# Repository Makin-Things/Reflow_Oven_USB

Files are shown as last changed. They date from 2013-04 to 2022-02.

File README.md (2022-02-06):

# Reflow Oven USB
This project converts a Mini Bake & Grill to be used as a reflow oven for soldering surfae mount pcb's. The oven was chosen for it's compact size but high power elements for its size. the even has been rewired to run both the top and bottom elements at the same time.

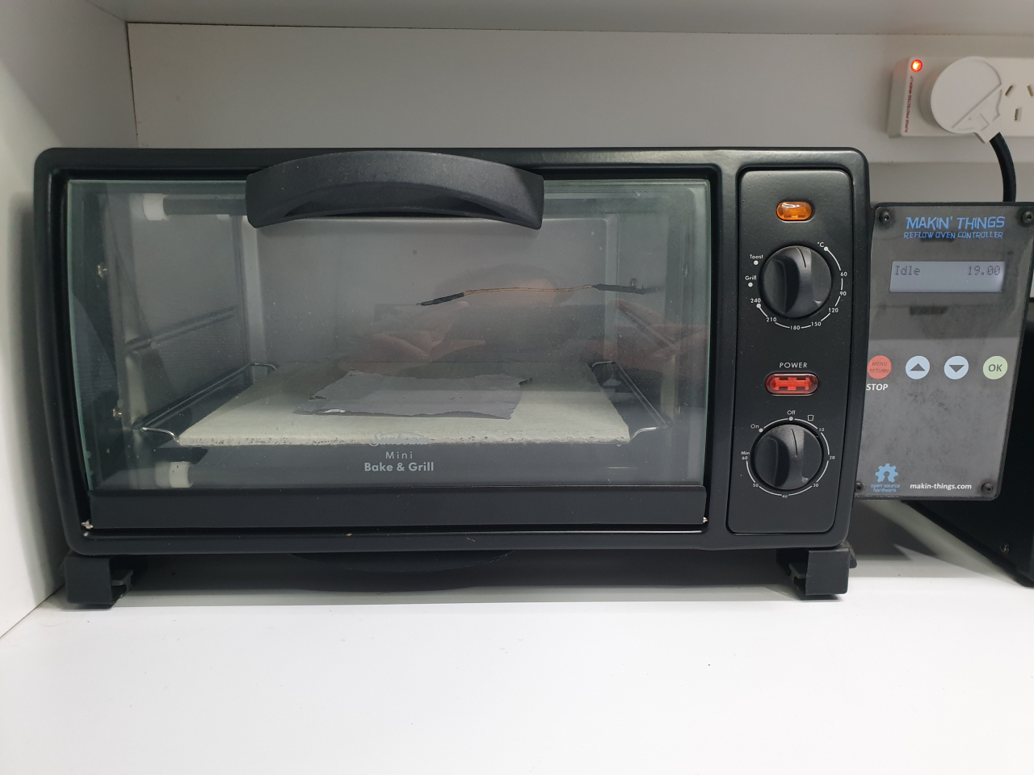
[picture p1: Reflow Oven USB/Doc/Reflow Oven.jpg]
Reflow Oven


The controller has a USB port to allow for firmware updates and monitoring/graphing of the oven while it is running profiles. See seperate repository SMD_Profiler for more information.

## Schematics

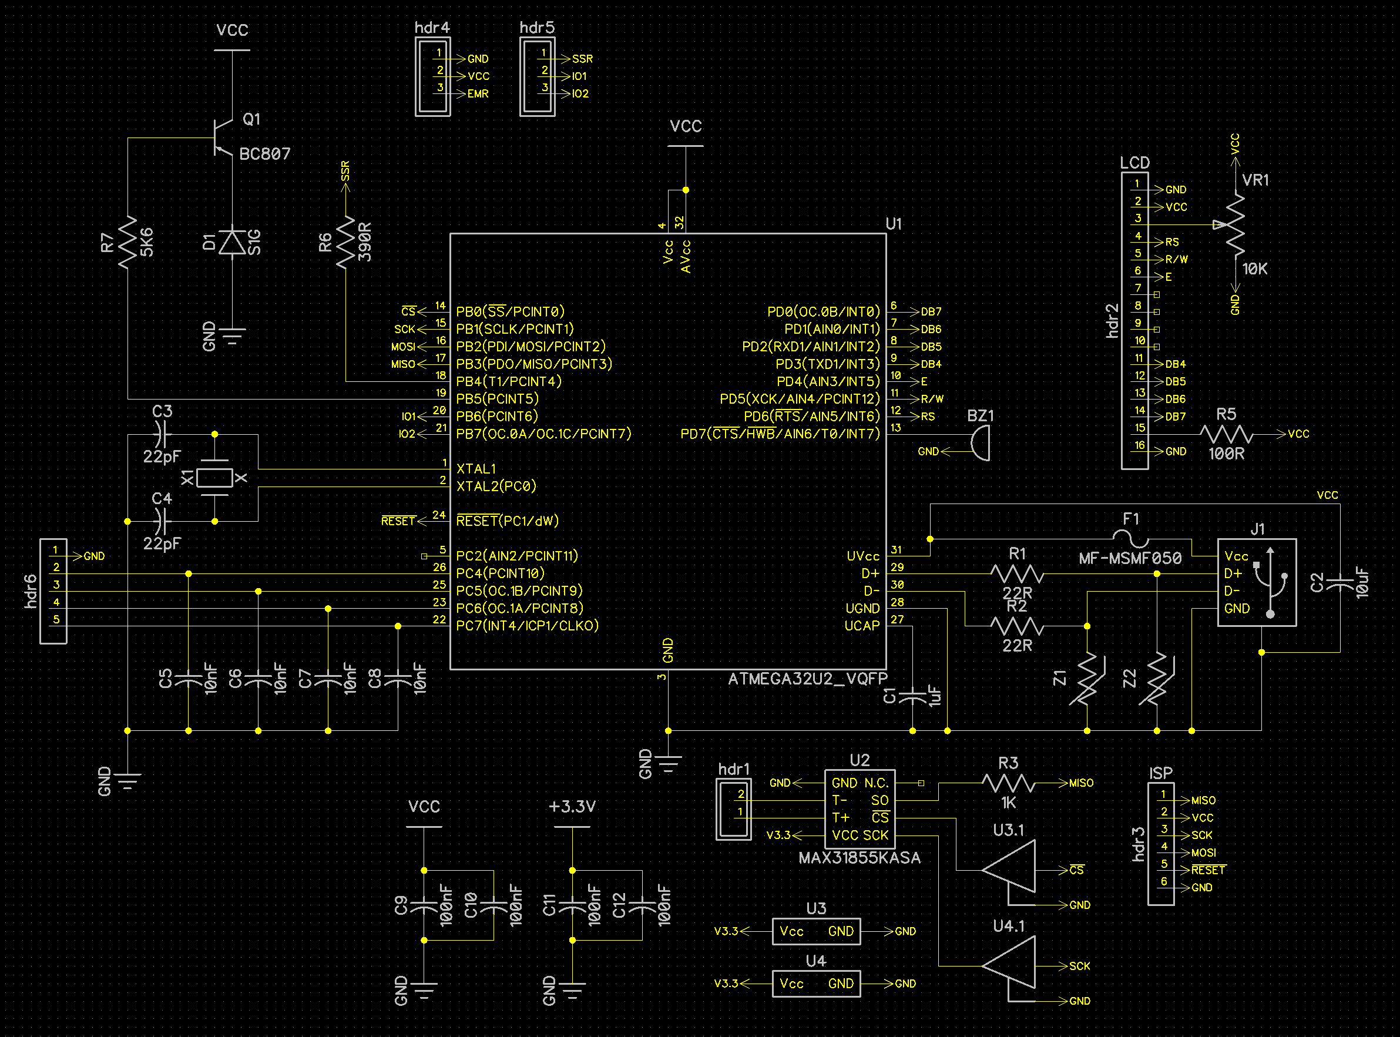
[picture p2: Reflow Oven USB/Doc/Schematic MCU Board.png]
MCU Board


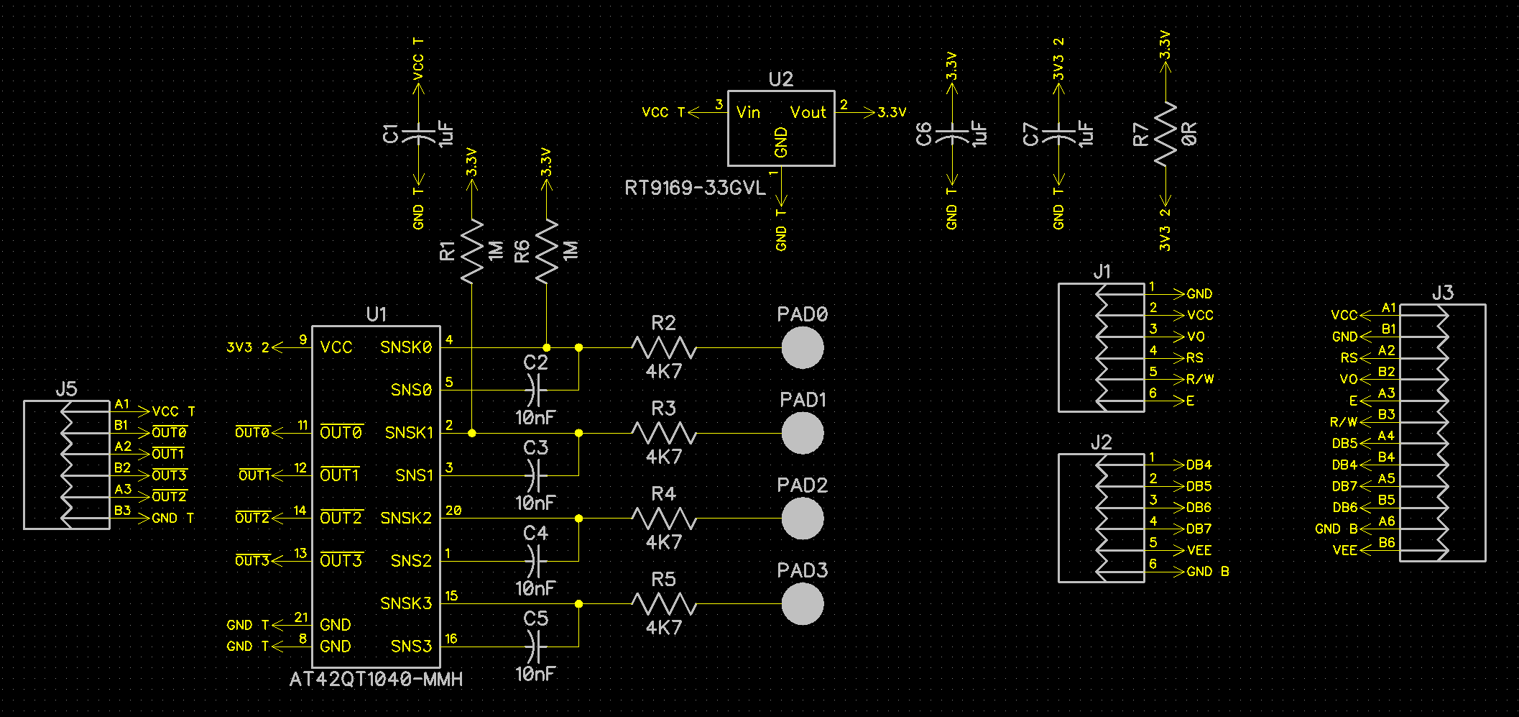
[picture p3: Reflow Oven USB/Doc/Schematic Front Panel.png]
Front Panel


## PCB Layouts

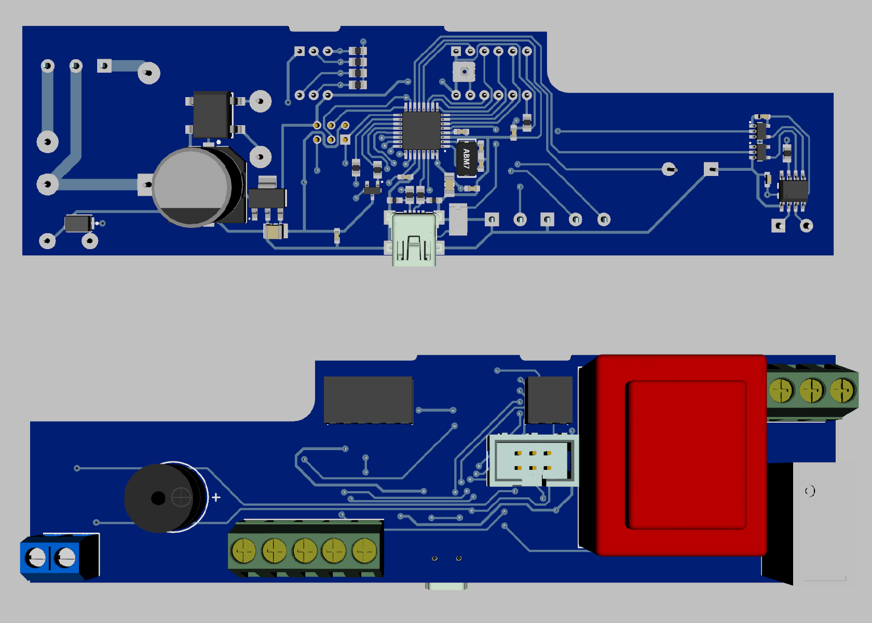
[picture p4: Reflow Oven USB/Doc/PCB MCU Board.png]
MCU Board


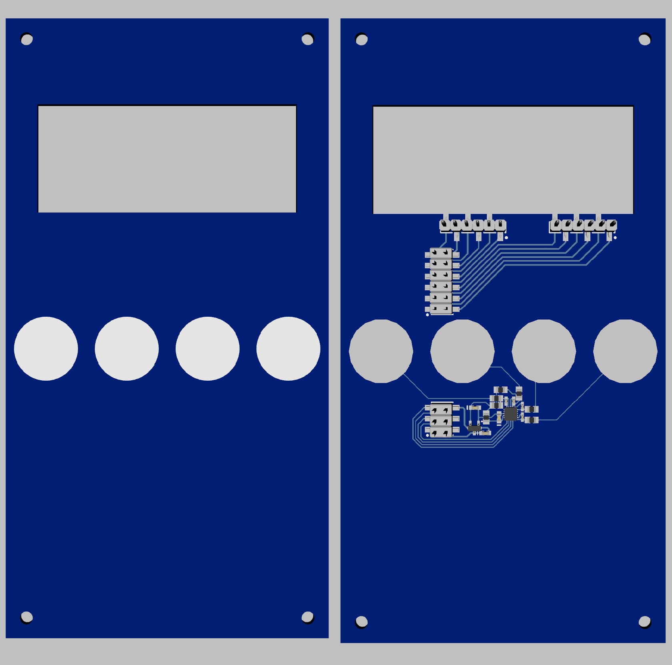
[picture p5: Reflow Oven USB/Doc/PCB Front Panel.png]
Front Panel


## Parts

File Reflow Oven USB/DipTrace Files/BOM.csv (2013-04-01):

RefDes | Type | Value | Part No
BZ1 | Buzzer |  | China
C1 | CAP_0603 | 1uF | E-9527699
C2 | CAP | 10uF | E-1639946
C3 | CAP_0603 | 22pF | E-1414622
C4 | CAP_0603 | 22pF | E-1414622
C5 | CAP_0603 | 10nF | E-1414609
C6 | CAP_0603 | 10nF | E-1414609
C7 | CAP_0603 | 10nF | E-1414609
C8 | CAP_0603 | 10nF | E-1414609
C9 | CAP_0603 | 100nF | E-1288255
C10 | CAP_0603 | 100nF | E-1288255
D1 | S1G |  | E-9843850
hdr1 | Screw Terminal2 |  | China
hdr2 | Hdr16 | LCD | E-3418479
hdr3 | Hdr2x3 | ISP | E-1348883
hdr4 | Screw Terminal3 |  | China
hdr5 | Screw Terminal3 |  | China
hdr6 | Hdr5 |  | Jaycar
J1 | USB Socket |  | E-1696539
J2 | JUMPER
Q1 | BC807 |  | E-1081219
R1 | RES_0805 | 22R | E-1738936
R2 | RES_0805 | 22R | E-1738936
R3 | RES_0805 | 1K | Jaycar
R4 | RES_0805 | 1K | Jaycar
R5 | RES_0805 | 8R2 | Jaycar
R6 | RES_0805 | 390R | Jaycar
R7 | RES_0805 | 5K6 | Jaycar
U1 | ATMEGA32U2_VQFP |  | E-1748524
U2 | MAX6675 |  | China
VR1 | POT | 10K | E-1689863
X1 | CRYSTAL | 8MHz | E-1812391

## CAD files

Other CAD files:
Inventor/Reflow Oven USB Hole.dwg
Inventor/Front Panels Polycarbonate.dwg
Inventor/Reflow Oven Mounting Holes.dwg
Inventor/Front Panels PCB.dwg
Inventor/Board.ipt
Inventor/Complete Reflow Oven.iam
Inventor/Imported Components/NHD-0216HZ/NHD-0216HZ.ipt
Inventor/Imported Components/Reflow Front/Board.ipt
Inventor/Imported Components/Reflow Front/Model_2.ipt
Inventor/Imported Components/Reflow Front/Model_5.ipt
Inventor/Imported Components/Reflow Front/Model_7.ipt
Inventor/Imported Components/Reflow Front/Reflow Front.iam
Inventor/Imported Components/Reflow Front/cap_0402.ipt
Inventor/Imported Components/Reflow Front/cap_0603.ipt
Inventor/Imported Components/Reflow Front/qfn-20_3x3x0.4.ipt
Inventor/Imported Components/Reflow Front/res_0805.ipt
Inventor/Imported Components/Reflow Front/sot23.ipt
Inventor/Imported Components/Reflow MCU/395443002.ipt
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

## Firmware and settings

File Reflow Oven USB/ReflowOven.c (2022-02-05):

//==============================================================================================================================
// U S B   R E F L O W   O V E N   C O N T R O L L E R
//
// Copyright	: 2011 ProAtomic Software Development Pty Ltd
// File Name	: "Reflow.c"
// Title 			: USB Reflow Oven Controller
// Date 			: 18 Jul 2011
// Version 		: 1.00
// Target MCU : ATMEGA32U2
// Author			: Simon Ratcliffe


//==============================================================================================================================
// Description of port usage
//
// Port/Bit	Direction	Usage
// --------	---------	----------------------------------------------------------------------------------------------------------
// B.0			Output		SPI SS for MAX6675
// B.1			Output		SPI Clock to MAX6675				(SCK)
// B.2			Output																(MOSI)
// B.3			Input			SPI Input from MAX6675			(MISO)
// B.4			Output		Dynamic Element Control (SSR)
// B.5			Output		Oven Power Cuttoff (EMR)
// B.6			Output		Spare output
// B.7			Output		Spare output
//
// C.4			Input			Switch 1
// C.5			Input			Switch 2
// C.6			Input			Switch 3
// C.7			Input			Switch 0
//
// D.0			Output		LCD DB4
// D.1			Output		LCD DB5
// D.2			Output		LCD DB6
// D.3			Output		LCD DB7
// D.4			Output		LCD RS
// D.5			Output		LCD R/W
// D.6			Output		LCD E
// D.7			Output		Buzzer

//==============================================================================================================================
// Includes

#include <avr/io.h>
#include <avr/wdt.h>
#include <avr/power.h>
#include <avr/interrupt.h>
#include <avr/pgmspace.h>
#include <string.h>
#include <stdio.h>
#include <stdlib.h>

#include "Descriptors.h"
#include "../LUFA/LUFA/Version.h"
#include "../LUFA/LUFA/Drivers/USB/USB.h"

#include "ReflowOven.h"
#include "lcd.h"
#include "spi.h"
#include "menu.h"
#include "pid.h"
//#include "version.h"

//==============================================================================================================================
// Protect against initial watchdog timeouts

void get_mcusr(void) __attribute__((naked)) __attribute__((section(".init3")));

void get_mcusr(void)
{
	MCUSR = 0;
	wdt_disable();
}

//==============================================================================================================================
// External variables

extern uint8_t CurrentMenuItemIdx;

//==============================================================================================================================
// Defines

#define buildstr "34"

#define OVEN_RELAY_SSR		PB4
#define OVEN_RELAY_EMR		PB5

#define EMR_ON						PORTB &= ~_BV(OVEN_RELAY_EMR)
#define EMR_OFF						PORTB |= _BV(OVEN_RELAY_EMR)

#define SSR_ON						PORTB |= _BV(OVEN_RELAY_SSR)
#define SSR_OFF						PORTB &= ~_BV(OVEN_RELAY_SSR)

//==============================================================================================================================
// Typedefs

typedef struct
{
	char name[PROFILE_NAME_LEN];
	unsigned char calibrated;
	unsigned char preheat_temp;
	unsigned char soak_dutycycle;
	unsigned char soak_rate;
	unsigned char soak_time;
	unsigned char soak_temp;
	unsigned char reflow_time;
	unsigned char reflow_temp;
	unsigned char preheat_cutoff;
	unsigned char reflow_cutoff;
} __profile;

//==============================================================================================================================
// EEPROM Variables and Data

uint8_t __attribute__((section(".validapp"))) ValidApp = 0xBB;

uint8_t EEMEM OvenCalibrated = 1;
uint8_t EEMEM ProfileCount = 3;

__profile EEMEM Profiles[MAX_PROFILES] = 
{
	{"Default         ",1,150,8,8,60,180,60,215,131,206},			  // for small low density boards
	{"Bigger Board    ",1,150,6,8,120,180,90,215,138,206},			// for larger high density boards
	{"Leadfree        ",1,150,12,8,120,200,120,255,138,248} 
};

//__profile EEMEM Profiles[MAX_PROFILES] = {{"Leadfree",1,150,3,2,200,120,255,138,248}}; //perfect for leaded solder
// original production profile that was used in the first 2 years __profile EEMEM Profiles[MAX_PROFILES] = {{"Default",1,150,2,4,180,90,215,124,204}};
// setup __profile EEMEM Profiles[MAX_PROFILES] = {{"Default",0,150,2,4,180,90,220,0,0}};
// 210 reflow __profile EEMEM Profiles[MAX_PROFILES] = {{"Default",1,150,2,4,180,90,210,123,199}};

uint8_t EEMEM TempCounts[20] = {18,14,14,15,11,10,11,11,10,12,11,12,12,11,12,13,18,15,16,16};
uint16_t EEMEM FinalTemps[20] = {77,117,153,185,213,237,257,0,0,0,0,0,0,0,0,0,0,0,0,0};

//==============================================================================================================================
// PROGMEM Menu definition

const MENU_ITEM ShowReflowMenu[];
const MENU_ITEM SettingsMenu[];
const MENU_ITEM SelectProfileMenu[];

const char Str00[] PROGMEM = "Main menu       ";
const char Str01[] PROGMEM = "Reflow          ";
const char Str02[] PROGMEM = "Settings        ";

const MENU_ITEM MainMenu[] PROGMEM = 
{
	{MENU_ITEM_TYPE_MAIN_MENU_HEADER, Str00, (PGM_P)SetIdleMode},
	{MENU_ITEM_TYPE_SUB_MENU, Str01, (PGM_P)ShowReflowMenu},
	{MENU_ITEM_TYPE_SUB_MENU, Str02, (PGM_P)SettingsMenu},
	{MENU_ITEM_TYPE_END_OF_MENU, NULL, 0}
};

const char Str10[] PROGMEM = "Reflow          ";
const char Str11[] PROGMEM = "Run             ";
const char Str12[] PROGMEM = "Select Profile  ";
const char Str13[] PROGMEM = "Edit Profile    ";

const MENU_ITEM ShowReflowMenu[] PROGMEM =
{	
	{MENU_ITEM_TYPE_SUB_MENU_HEADER, Str10, (PGM_P)MainMenu},
	{MENU_ITEM_TYPE_COMMAND, Str11, (PGM_P)RunProfileCommand},
	{MENU_ITEM_TYPE_SUB_MENU, Str12, (PGM_P)SelectProfileMenu},
	{MENU_ITEM_TYPE_COMMAND, Str13, (PGM_P)EditProfileCommand},
	{MENU_ITEM_TYPE_END_OF_MENU, NULL, 0}
};

const char Str200[] PROGMEM = "Select Profile  ";

const MENU_ITEM SelectProfileMenu[] PROGMEM =
{
	{MENU_ITEM_TYPE_SUB_MENU_HEADER, Str200, (PGM_P)ShowReflowMenu},
	{MENU_ITEM_TYPE_EEMEM_COMMAND, (PGM_P)MenuGetEEMEMItem, (PGM_P)SelectProfileCommand}
};	

const char Str20[] PROGMEM = "Settings        ";
const char Str21[] PROGMEM = "Calib. Oven     ";
const char Str22[] PROGMEM = "PID Test        ";
const char Str23[] PROGMEM = "Calib. Profile  ";
const char Str24[] PROGMEM = "Calib. 60c      ";
const char Str25[] PROGMEM = "Calib. 120c     ";

const MENU_ITEM SettingsMenu[] PROGMEM =
{
	{MENU_ITEM_TYPE_SUB_MENU_HEADER, Str20, (PGM_P)MainMenu},
	{MENU_ITEM_TYPE_COMMAND, Str21, (PGM_P)CalibrateOvenCommand},
	{MENU_ITEM_TYPE_COMMAND, Str22, (PGM_P)PIDTestCommand},
	{MENU_ITEM_TYPE_COMMAND, Str23, (PGM_P)CalibrateProfileCommand},
	{MENU_ITEM_TYPE_COMMAND, Str24, (PGM_P)Calibrate60cCommand},
	{MENU_ITEM_TYPE_COMMAND, Str25, (PGM_P)Calibrate120cCommand},
	{MENU_ITEM_TYPE_END_OF_MENU, NULL, 0}
};

// Oven calibration stages

// Profile calibration stages

// Reflow stages

//==============================================================================================================================
// Global Variables

USB_ClassInfo_CDC_Device_t VirtualSerial_CDC_Interface =
{
	.Config =
	{
		.ControlInterfaceNumber   = 0,
		.DataINEndpoint           =
		{
			.Address          = CDC_TX_EPADDR,
			.Size             = CDC_TXRX_EPSIZE,
			.Banks            = 1,
		},
		.DataOUTEndpoint =
		{
			.Address          = CDC_RX_EPADDR,
			.Size             = CDC_TXRX_EPSIZE,
			.Banks            = 1,
		},
		.NotificationEndpoint =
		{
			.Address          = CDC_NOTIFICATION_EPADDR,
			.Size             = CDC_NOTIFICATION_EPSIZE,
			.Banks            = 1,
		},
	},
};

static FILE USBSerialStream;
char inBuf[80];
char tmpStr[17];
char profileName[PROFILE_NAME_LEN];
uint8_t currentProfile = 1;
bool usbConnected = false;
bool isRunning = false;
bool showTemp = true;
uint32_t ovenTempAccum = 0;
uint16_t ovenTemp;
uint16_t ovenEndTemp;
uint16_t ovenTempArray[68];
uint16_t ovenDelta4Array[12] = {0xFFFF};
int16_t ovenDelta4;
int16_t ovenDelta16;
int16_t ovenDelta32;
int16_t ovenRateOfChange;
uint8_t deltaCount = 0;
uint8_t ovenStage; // Used to store where a task is up to
uint16_t ovenCounter;
int16_t ovenError = 0;
void(*ProcessHandler)();
uint16_t count = 0;
uint16_t endCount = 3600;
uint8_t endSet = 0;
__profile profile;
volatile uint8_t tick = 0;
volatile bool readtick = 0;
volatile uint8_t subtickCounter = 0;
volatile uint8_t duty_cycle = 0;
uint8_t readings = 0;
bool lcdPresent = true;
uint8_t buttons = 0;
uint8_t newButton;
PIDController pid;

//==============================================================================================================================
// Interrupt routines

ISR (TIMER1_COMPA_vect)
{
	subtickCounter++;
	if (subtickCounter == 100)
	{
		subtickCounter = 0;
	}

	if ((subtickCounter % 10) == 0)
	{
		readtick = ((subtickCounter % 10) == 0);
	}

  if ((subtickCounter == 0) || (subtickCounter == 50))
	{
		tick++;
	}
	
	if ((duty_cycle > 0) && (duty_cycle < 100))
	{
		if (subtickCounter == duty_cycle)
		{
			SSR_OFF;
		}
		else if (subtickCounter == 0)
		{
			SSR_ON;
		}
	}
}

//==============================================================================================================================
// Get the menu item at a given index from EEMEM

void MenuGetEEMEMItem(uint8_t idx)
{
	eeprom_read_block ((void*)&profileName, (const void*)&Profiles[idx-1], PROFILE_NAME_LEN);
}

//==============================================================================================================================
// Event handler for the library USB Connection event

void EVENT_USB_Device_Connect(void)
{
	usbConnected = true;
}

//==============================================================================================================================
// Event handler for the library USB Disconnection event

void EVENT_USB_Device_Disconnect(void)
{
	usbConnected = false;
}

//==============================================================================================================================
// Event handler for the library USB Configuration Changed event

void EVENT_USB_Device_ConfigurationChanged(void)
{
	bool ConfigSuccess = true;

	ConfigSuccess &= CDC_Device_ConfigureEndpoints(&VirtualSerial_CDC_Interface);
}

//==============================================================================================================================
// Event handler for the library USB Control Request reception event

void EVENT_USB_Device_ControlRequest(void)
{
	CDC_Device_ProcessControlRequest(&VirtualSerial_CDC_Interface);
}

//==============================================================================================================================
// Functions

uint8_t GetPacket(char* buf, uint8_t size)
{
	if (CDC_Device_BytesReceived(&VirtualSerial_CDC_Interface))
	{
		fgets(buf, size, &USBSerialStream);
//		printf("$$%s$$\n", buf);
		while ((strlen(buf) > 0) && ((buf[strlen(buf)-1] == '\r') || (buf[strlen(buf)-1] == '\n')))
		{
			buf[strlen(buf)-1] = 0;
		}
//		printf("##%s##\n", inBuf);
		return true;
	}
	
	return false;
}

//==============================================================================================================================
// Configure the various bits of hardware

void SetupHardware(void)
{
	// Configure IO Ports
	PORTB = _BV(OVEN_RELAY_EMR); // Turn off the EMR relay
	DDRB |= _BV(OVEN_RELAY_SSR) | _BV(OVEN_RELAY_EMR); // Relay outputs
	DDRD |= _BV(PD7); // Buzzer as output
	PORTC = 0xF0; // Enable pullups on for switches

	// Initialise SPI
  spi_init ();

	//Initialise LCD
  if (!lcd_init (LCD_DISP_ON)) // Initialise the LCD
  {
	  lcdPresent = false;
  }

	// USB Hardware Initialization
	USB_Init();
	
	// Setup Timer/Counter1
	TCCR1A = 0;
	TCCR1B = (1 << WGM12) | (1 << CS11) | (1 << CS10);
	OCR1A = 1250; // = 0.01 seconds
//	OCR1A = 6250; // = 0.05 seconds
//	OCR1A = 12500; // = 0.1 seconds
//	OCR1A = 62500; // = 0.5 seconds
	TIMSK1 = (1 << OCIE1A);
}

//==============================================================================================================================
// Read temperature
uint16_t ReadTemp ()
{
  return spi_read();	
}


//==============================================================================================================================
// Send a temperature packet

void UpdateTemp (void)
{
	char str[20];

	ovenTemp = ovenTempAccum>>2;
	ovenTempAccum = 0;
	
	if (ovenTempArray[0] == 0)
	{
		for (uint8_t i = 0; i < 68; i++)
		{
			ovenTempArray[i] = ovenTemp;
		}
	}
	else
	{
		memmove(&ovenTempArray[1], &ovenTempArray[0], sizeof(uint16_t)*67);
		ovenTempArray[0] = ovenTemp;
	}
	
	ovenDelta4 = (int16_t)(ovenTempArray[0]+ovenTempArray[1]+ovenTempArray[2]+ovenTempArray[3]-ovenTempArray[8]-ovenTempArray[9]-ovenTempArray[10]-ovenTempArray[11]);
	ovenDelta16 = (int16_t)(ovenTempArray[0]+ovenTempArray[1]+ovenTempArray[2]+ovenTempArray[3]-ovenTempArray[32]-ovenTempArray[33]-ovenTempArray[34]-ovenTempArray[35]);
	ovenDelta32 = (int16_t)(ovenTempArray[0]+ovenTempArray[1]+ovenTempArray[2]+ovenTempArray[3]-ovenTempArray[64]-ovenTempArray[65]-ovenTempArray[66]-ovenTempArray[67]);

	if (ovenDelta4Array[0] == 0xFFFF)
	{
		for (uint8_t i = 0; i < 12; i++)
		{
			ovenDelta4Array[i] = ovenDelta4;
		}
	}
	else
	{
		memmove(&ovenDelta4Array[1], &ovenDelta4Array[0], sizeof(uint16_t)*11);
		ovenDelta4Array[0] = ovenDelta4;
	}
	
	ovenRateOfChange = (int16_t)(ovenDelta4Array[0]+ovenDelta4Array[1]+ovenDelta4Array[2]+ovenDelta4Array[3]-ovenDelta4Array[8]-ovenDelta4Array[9]-ovenDelta4Array[10]-ovenDelta4Array[11]);

	if (lcdPresent)
	{
		lcd_gotoxy(10, 0);
	}

	if (ovenTemp >= 65533)
	{
	  setDutyCycle(0); //Turn off SSR
	  _delay_ms(25); //Wait for SSR to power down
	  EMR_OFF; // Turn off EMR
		if (ovenTemp == 65535)
		{
			sprintf_P (str, PSTR("No TC "));
		}
		else if (ovenTemp == 65534)			
		{
			sprintf_P (str, PSTR("SG Err"));
		}
		else
		{
			sprintf_P (str, PSTR("SV Err"));
		}
		if ((lcdPresent) && (showTemp))
		{
			lcd_puts (str);
		}		
		fprintf (&USBSerialStream, "%u,%u,%s\n", ovenStage, count, str);
	}
	else
	{
		sprintf_P (str, PSTR("%3u.%02u"), ovenTemp>>2, (ovenTemp & 0x03)*25);
		if ((lcdPresent) && (showTemp))
		{
			lcd_puts (str);
		}
		fprintf_P (&USBSerialStream, PSTR("%u,%u,%s,%u, %d,%d,%d, %d,%d\n"), ovenStage, count, str, duty_cycle, ovenDelta4, ovenDelta16, ovenDelta32, ovenRateOfChange, ovenError);
	}

	count++;
}

//==============================================================================================================================
// Send the oven settings

void SendOvenSettings(void)
{
	char ReportString[80];
	
	sprintf_P(ReportString, PSTR("=OGET,%u,%u,%u"), eeprom_read_byte(&OvenCalibrated), MAX_PROFILES, eeprom_read_byte(&ProfileCount));
	for (uint8_t i = 0; i < 20; i++)
	{
		sprintf_P(tmpStr, PSTR(",%u"), eeprom_read_byte(&TempCounts[i]));
		strcat(ReportString, tmpStr);
	}
	
	strcat(ReportString,"\n");
	
	// Write the string to the virtual COM port via the created character stream
	fputs(ReportString, &USBSerialStream);
}

//==============================================================================================================================
// Cleanup and jump into the bootloader

void Bootloader(void)
{
	lcd_clrscr();
	lcd_puts_P("Bootloader");
//	wdt_disable();
	TIMSK1 = 0; // Disable TIMER1
	USB_Detach();
	_delay_ms(1000);
	eeprom_write_byte(&ValidApp, 0xFF);
	while (!eeprom_is_ready());
	wdt_enable(WDTO_30MS);
	for (;;);
}

//==============================================================================================================================
//

void setDutyCycle (uint8_t ratio)
{
	duty_cycle = ratio;
	if (duty_cycle == 0)
	{
		SSR_OFF;
	}
	if (duty_cycle == 100)
	{
		SSR_ON;
	}
}

//==============================================================================================================================
//

uint8_t getDutyCycle(uint16_t temp)
{
	uint8_t i;
	
	for (i = 0; i < 20; i++)
	{
		if (temp <= eeprom_read_word(&FinalTemps[i]))
		{
			return (i+1)*5;
		}
	}
	return 0;
}

//==============================================================================================================================
//

void printProfile (void)
{
	fprintf (&USBSerialStream, "=RUN,%s,%u,%u,%u,%u,%u,%u,%u,%u\n",
		profile.name, profile.preheat_temp, profile.soak_dutycycle*5, profile.soak_temp, profile.reflow_time, profile.reflow_temp, profile.calibrated,
		profile.preheat_cutoff, profile.reflow_cutoff);
}

//==============================================================================================================================
//

void RunProfileCommand()
{
	lcd_gotoxy(0, 1);
	lcd_puts_P("                ");
	showTemp = true;
	ovenStage = 0;
	count = 0;
	ProcessHandler = RunProfileHandler;
	isRunning = true;
};

//==============================================================================================================================
//

void RunProfileHandler()
{
	switch (ovenStage)
	{
		case 0: // close door & start message
			lcd_gotoxy(0, 1);
			lcd_puts_P("Close door      ");
			ovenStage++;
			break;

		case 1: // wait for button press
			if ((newButton) && (buttons == EVENT_ENTER_BUTTON_PUSHED))
			{
				ovenStage++;
			}
			break;

		case 2: // Preheat
			printProfile(); // Send the profile we are about to run to the serial port
			lcd_gotoxy(0, 1);
			lcd_puts_P("Preheat         ");
			count = 0;
			EMR_ON; //Turn on the EMR
			_delay_ms(25);
			setDutyCycle(100); //Turn on the SSR
			ovenStage++;
			break;

		case 3: // Reached preheat cutoff
//			if ((ovenTemp >> 2) >= profile.preheat_cutoff)
			if ((ovenTemp) >= ((profile.preheat_temp << 2) - ovenDelta4))
			{
				lcd_gotoxy(0, 1);
				lcd_puts_P("Preheat cutoff  ");
				setDutyCycle(getDutyCycle(profile.preheat_temp)-5); //Reduce the output power
				ovenStage++;
			}
			break;

		case 4: // Wait for the oven to reach the preheat temp
			if ((ovenTemp >> 2) >= profile.preheat_temp)
			{
				lcd_gotoxy(0, 1);
				lcd_puts("Soak            ");
				ovenCounter = 0;
				ovenStage++;
			}
			break;

		case 5:
			if (tick)
			{
				ovenCounter++;
				ovenError = (int16_t)(ovenTemp-(((uint16_t)(profile.preheat_temp) << 2)+(((uint16_t)profile.soak_temp-(uint16_t)profile.preheat_temp) << 2)*((float)(ovenCounter)/((uint16_t)profile.soak_time << 1))));
				
				if (ovenError > 8) // rate to high, reduce duty cycle
				{
					setDutyCycle(getDutyCycle(profile.soak_temp));
				}
				else
				{
					setDutyCycle(getDutyCycle(profile.soak_temp)+abs(ovenError-12)*5/4);
				}

				if ((ovenTemp >> 2) >= profile.soak_temp)
				{
					setDutyCycle(100);
					lcd_gotoxy(0, 1);
					lcd_puts_P("Reflow          ");
					ovenCounter = count;
					ovenError = 0;
					ovenStage++;
				}
			}
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
int main(void)
{
	SetupHardware();
	
	// Create a regular character stream for the interface so that it can be used with the stdio.h functions
	CDC_Device_CreateStream(&VirtualSerial_CDC_Interface, &USBSerialStream);

	sei();

	if (lcdPresent)
	{
	  lcd_clrscr(); // clear display and home cursor
		lcd_puts_P("Reflow Oven USB\nv2."buildstr);
	}

	for (;;)
	{
		if (tick == 6)
		{
			if (lcdPresent)
			{
				lcd_clrscr(); // clear display and home cursor
			}
			// Check oven is calibrated
			if (!eeprom_read_byte(&OvenCalibrated))
			{
				if (lcdPresent)
				{
					lcd_puts_P("Oven\nNot calibrated");
				}
			}
			else // read profiles
			{
				sprintf_P(tmpStr, PSTR("Profiles %02u/%02u"), 0, eeprom_read_byte(&ProfileCount));
				if (lcdPresent)
				{
					lcd_puts_P("Oven Calibrated");
					lcd_gotoxy(0, 1);
					lcd_puts(tmpStr);
				}
				tick++;
			}
		}
		else if (tick == 13)		
		{
			if (lcdPresent)
			{
			  lcd_clrscr(); // clear display and home cursor
			}
			tick = 0;
			break;
		}
		
		if (GetPacket(inBuf, sizeof(inBuf))) // Check if there is incoming USB data
		{
			ProcessPacket(inBuf);
		}
		
		CDC_Device_USBTask(&VirtualSerial_CDC_Interface);
		USB_USBTask();
	}

	// Load the default profile
	eeprom_read_block((void*)&profile, (const void*)&Profiles[0], sizeof(__profile));
	
	SetIdleMode();

	for (;;)
	{
		if ((newButton = ReadButtons()))
		{
			if ((buttons == EVENT_MENU_BUTTON_PUSHED) && (isRunning)) // Turn the oven off and go back to idle
			{ 
				setDutyCycle(0); //Turn off the SSR
				_delay_ms(25);
				EMR_OFF; //Turn off the EMR
				fprintf(&USBSerialStream, "=ABORT\n");
				isRunning = false;
				ovenStage = 0;
				SetIdleMode();
			}
			else if ((buttons != 0) && (!isRunning) && (lcdPresent)) // Only allow the use of menus if there is an LCD
			{
				MenuExecuteEvent(buttons);
			}
		}
		
		if (readtick)
		{
			if (readings < 4)
			{
				ovenTempAccum += ReadTemp();
				readings++;
			}
			readtick = 0;
		}

		if (isRunning)
		{
			(*ProcessHandler)();
		}

		if (tick)
		{
			UpdateTemp();
			tick = 0;
			readings = 0;
		}
		
		if (GetPacket(inBuf, sizeof(inBuf))) // Check if there is incoming USB data
		{
			ProcessPacket(inBuf);
		}

		CDC_Device_USBTask(&VirtualSerial_CDC_Interface);
		USB_USBTask();
		_delay_ms(10);
	}
}

//==============================================================================================================================

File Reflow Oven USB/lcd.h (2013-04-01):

#ifndef LCD_H
#define LCD_H
/*************************************************************************
 Title	:   C include file for the HD44780U LCD library (lcd.c)
 Author:    Peter Fleury <pfleury@gmx.ch>  http://jump.to/fleury
 File:	    $Id: lcd.h,v 1.13.2.2 2006/01/30 19:51:33 peter Exp $
 Software:  AVR-GCC 3.3
 Hardware:  any AVR device, memory mapped mode only for AT90S4414/8515/Mega
***************************************************************************/

/**
 @defgroup pfleury_lcd LCD library
 @code #include <lcd.h> @endcode
 
 @brief Basic routines for interfacing a HD44780U-based text LCD display

 Originally based on Volker Oth's LCD library,
 changed lcd_init(), added additional constants for lcd_command(), 
 added 4-bit I/O mode, improved and optimized code.
       
 Library can be operated in memory mapped mode (LCD_IO_MODE=0) or in 
 4-bit IO port mode (LCD_IO_MODE=1). 8-bit IO port mode not supported.

 Memory mapped mode compatible with Kanda STK200, but supports also 
 generation of R/W signal through A8 address line.
       
 @author Peter Fleury pfleury@gmx.ch http://jump.to/fleury
 
 @see The chapter <a href="http://homepage.sunrise.ch/mysunrise/peterfleury/avr-lcd44780.html" target="_blank">Interfacing a HD44780 Based LCD to an AVR</a>
      on my home page.

*/

/*@{*/

#if (__GNUC__ * 100 + __GNUC_MINOR__) < 303
#error "This library requires AVR-GCC 3.3 or later, update to newer AVR-GCC compiler !"
#endif

#include <inttypes.h>
#include <avr/pgmspace.h>

/** 
 *  @name  Definitions for MCU Clock Frequency
 *  Adapt the MCU clock frequency in Hz to your target. 
 */
#define XTAL F_CPU              /**< clock frequency in Hz, used to calculate delay timer */


/**
 * @name  Definition for LCD controller type
 * Use 0 for HD44780 controller, change to 1 for displays with KS0073 controller.
 */
#define LCD_CONTROLLER_KS0073 0  /**< Use 0 for HD44780 controller, 1 for KS0073 controller */

/** 
 *  @name  Definitions for Display Size 
 *  Change these definitions to adapt setting to your display
 */
#define LCD_LINES           2     /**< number of visible lines of the display */
#define LCD_DISP_LENGTH    16     /**< visibles characters per line of the display */
#define LCD_LINE_LENGTH  0x40     /**< internal line length of the display    */
#define LCD_START_LINE1  0x00     /**< DDRAM address of first char of line 1 */
#define LCD_START_LINE2  0x40     /**< DDRAM address of first char of line 2 */
#define LCD_START_LINE3  0x14     /**< DDRAM address of first char of line 3 */
#define LCD_START_LINE4  0x54     /**< DDRAM address of first char of line 4 */
#define LCD_WRAP_LINES      0     /**< 0: no wrap, 1: wrap at end of visibile line */


#define LCD_IO_MODE      1         /**< 0: memory mapped mode, 1: IO port mode */
#if LCD_IO_MODE
/**
 *  @name Definitions for 4-bit IO mode
 *  Change LCD_PORT if you want to use a different port for the LCD pins.
 *
 *  The four LCD data lines and the three control lines RS, RW, E can be on the 
 *  same port or on different ports. 
 *  Change LCD_RS_PORT, LCD_RW_PORT, LCD_E_PORT if you want the control lines on
 *  different ports. 
 *
 *  Normally the four data lines should be mapped to bit 0..3 on one port, but it
 *  is possible to connect these data lines in different order or even on different
 *  ports by adapting the LCD_DATAx_PORT and LCD_DATAx_PIN definitions.
 *  
 */
#define LCD_PORT         PORTD        /**< port for the LCD lines   */
#define LCD_DATA0_PORT   LCD_PORT     /**< port for 4bit data bit 0 */
#define LCD_DATA1_PORT   LCD_PORT     /**< port for 4bit data bit 1 */
#define LCD_DATA2_PORT   LCD_PORT     /**< port for 4bit data bit 2 */
#define LCD_DATA3_PORT   LCD_PORT     /**< port for 4bit data bit 3 */
#define LCD_DATA0_PIN    3            /**< pin for 4bit data bit 0  */
#define LCD_DATA1_PIN    2            /**< pin for 4bit data bit 1  */
#define LCD_DATA2_PIN    1            /**< pin for 4bit data bit 2  */
#define LCD_DATA3_PIN    0            /**< pin for 4bit data bit 3  */
#define LCD_E_PORT       LCD_PORT			/**< port for Enable line     */
#define LCD_E_PIN        4            /**< pin  for Enable line     */
#define LCD_RW_PORT      LCD_PORT     /**< port for RW line         */
#define LCD_RW_PIN       5            /**< pin  for RW line         */
#define LCD_RS_PORT      LCD_PORT     /**< port for RS line         */
#define LCD_RS_PIN       6            /**< pin  for RS line         */

#elif defined(__AVR_AT90S4414__) || defined(__AVR_AT90S8515__) || defined(__AVR_ATmega64__) || \
      defined(__AVR_ATmega8515__)|| defined(__AVR_ATmega103__) || defined(__AVR_ATmega128__) || \
      defined(__AVR_ATmega161__) || defined(__AVR_ATmega162__)
/*
 *  memory mapped mode is only supported when the device has an external data memory interface
 */
#define LCD_IO_DATA      0xC000    /* A15=E=1, A14=RS=1                 */
#define LCD_IO_FUNCTION  0x8000    /* A15=E=1, A14=RS=0                 */
#define LCD_IO_READ      0x0100    /* A8 =R/W=1 (R/W: 1=Read, 0=Write   */
#else
#error "external data memory interface not available for this device, use 4-bit IO port mode"

#endif


/**
 *  @name Definitions for LCD command instructions
 *  The constants define the various LCD controller instructions which can be passed to the 
 *  function lcd_command(), see HD44780 data sheet for a complete description.
 */

/* instruction register bit positions, see HD44780U data sheet */
#define LCD_CLR               0      /* DB0: clear display                  */
#define LCD_HOME              1      /* DB1: return to home position        */
#define LCD_ENTRY_MODE        2      /* DB2: set entry mode                 */
#define LCD_ENTRY_INC         1      /*   DB1: 1=increment, 0=decrement     */
#define LCD_ENTRY_SHIFT       0      /*   DB2: 1=display shift on           */
#define LCD_ON                3      /* DB3: turn lcd/cursor on             */
#define LCD_ON_DISPLAY        2      /*   DB2: turn display on              */
#define LCD_ON_CURSOR         1      /*   DB1: turn cursor on               */
#define LCD_ON_BLINK          0      /*     DB0: blinking cursor ?          */
#define LCD_MOVE              4      /* DB4: move cursor/display            */
#define LCD_MOVE_DISP         3      /*   DB3: move display (0-> cursor) ?  */
#define LCD_MOVE_RIGHT        2      /*   DB2: move right (0-> left) ?      */
#define LCD_FUNCTION          5      /* DB5: function set                   */
#define LCD_FUNCTION_8BIT     4      /*   DB4: set 8BIT mode (0->4BIT mode) */
#define LCD_FUNCTION_2LINES   3      /*   DB3: two lines (0->one line)      */
#define LCD_FUNCTION_10DOTS   2      /*   DB2: 5x10 font (0->5x7 font)      */
#define LCD_CGRAM             6      /* DB6: set CG RAM address             */
#define LCD_DDRAM             7      /* DB7: set DD RAM address             */
#define LCD_BUSY              7      /* DB7: LCD is busy                    */
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

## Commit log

2013-04-01 Initial import
    [BOM.csv, BOM.xlsx]
2014-08-31 Updated USB VID/PID.
2014-08-31 Added Windows INF Driver/Reflow Oven.inf
2014-09-01 Shuffled buttons to the correct order.
    [ReflowOven.c]
2014-12-31 Added an extra profile for a leaded solder board with more thermal mass.
2014-12-31 Update to oven calibaration code. Add a bit more heat during the reflow cutoff.
2014-12-31 Update bigger board profile to extend soak period
2015-01-01 Added v2 schematic and pcb designs.
2015-01-01 Add inventor files.
    [395443002.ipt, Board.ipt, Buzzer.ipt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]
2015-01-03 Added code for overshoot estimation (=O120).
    [ReflowOven.c]
2015-01-22 Added new calibration procedure.
2015-01-23 Rework to get oven profiles running better. Not yet complete.
    [ReflowOven.c]
2022-02-05 Add constant 60c for filament drying
2022-02-05 Add constant 60c for filament drying.
2022-02-06 Added more images for documentation.
    [Complete Reflow Oven.iam]
